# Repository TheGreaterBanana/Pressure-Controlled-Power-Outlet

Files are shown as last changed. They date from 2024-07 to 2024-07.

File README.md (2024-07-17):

# Pressure-Controlled-Power-Outlet
This is my (for sure) late Birthday present for my mom:

The idea for this project is that she have a water bin that holds water off of the roof of her house. Which my mother uses to water her gardens. The problem is that the pump she uses does not stop when the pressure starts to build!

So this is ment to fix this by using a water pressure sensor to see when the hose nozzel is closed by detecting a large jump in pressure then disablling the outlet that is powering the pump. Then when the nozzel is opened again this will detect the drop in pressure and re-enable the outlet.

This respository will have the code for the pico (RP2040) microcontroller, the schematics for the PCB and the case that will be used. 

The design philosophy for this project is to have everything as simple and cheap as possible, for this as many components as possible will be through hole as I dont want to pay to have parts placed on the pcb. If a part has to be surface mount it will have a extra large footprint to make it as easy as possible to assemble.

The specs:
    - 125V
    - 20A
    - GFCI protected outlets
    - Useable outdoors

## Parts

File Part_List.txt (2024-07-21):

This is the part list for the Pressure Controlled Power Outlet

digikey:
    Note: This is overkill but it was a 24V internal PSU that I had on hand
	Mornsun America LM100-23B24R2-C https://www.digikey.ca/en/products/detail/mornsun-america-llc/LM100-23B24R2-C/18108181 x1

HomeDepot:
    Leviton 20 Amp Self-Test SmartlockPro Slim Duplex GFCI Outlet https://www.homedepot.ca/product/leviton-20-amp-self-test-smartlockpro-slim-duplex-gfci-outlet-in-black/1001791826    x1

Mouser:
    Nichicon UCY2G120MPD 12µF Cap https://www.mouser.ca/ProductDetail/647-UCY2G120MPD                       x1
    STMicroelectronics LD1085V50 5V 3A LDO https://www.mouser.ca/ProductDetail/511-LD1085V50                x1
    TE Connectivity T9GS1L24-24 Relay https://www.mouser.ca/ProductDetail/655-T9GS1L24-24                   x1
    DFRobot SEN0257 Analog Water Pressure Sensor https://www.mouser.ca/ProductDetail/426-SEN0257            x2
    Io Audio IO-C20SP-63 C20 PEM https://www.mouser.ca/ProductDetail/670-IO-C20SP-63                        x1
    Raspberry Pi SC0918 Pico W https://www.mouser.ca/ProductDetail/358-SC0918                               x1
    Texas Instruments LM324AN/NOPB https://www.mouser.ca/ProductDetail/926-LM324AN-NOPB                     x1
    Vishay MBB02070C3302FCT00 33k Ohm Resistor https://www.mouser.ca/ProductDetail/594-MBB02070C3302FCT     x1
    YAGEO MFR-12FTF52-17K 17K Ohm Resistor https://www.mouser.ca/ProductDetail/603-MFR-12FTF52-17K          x1
    KOA Speer MF1/4LCT52R561G 560 Ohm Resistor https://www.mouser.ca/ProductDetail/660-MF1-4LCT52R561G      x4
    Infineon IRF540NPBF MOSFET https://www.mouser.ca/ProductDetail/942-IRF540NPBF                           x2
    Diotec Semiconductor 2N3906 Transistor https://www.mouser.ca/ProductDetail/637-2N3906                   x2
    Vishay 1N5405-E3/54 Diode https://www.mouser.ca/ProductDetail/625-1N5405-E3                             x2
    Phoenix Contact 1017514 PCB PWR Connector https://www.mouser.ca/ProductDetail/651-1017514               x1
    Diotec Semiconductor 2N3904 Transistor https://www.mouser.ca/ProductDetail/637-2N3904                   x4
    YAGEO MFR1WSFTE52-10K 10K Ohm Resistor https://www.mouser.ca/ProductDetail/603-MFR1WSFTE52-10K          x10
    Molex 47053-3000 4-Pin PWM Connector https://www.mouser.ca/ProductDetail/538-47053-3000                 x2
    Rubycon 80ZLH220MEFC10X23 220µF Cap https://www.mouser.ca/ProductDetail/232-80ZLH220MEFC10X2            x1
    KEMET ESL476M100AH9AA 47µF Cap https://www.mouser.ca/ProductDetail/80-ESL476M100AH9AA                   x1
    Harwin M7581-46 Jumper https://www.mouser.ca/ProductDetail/855-M7581-46                                 x2

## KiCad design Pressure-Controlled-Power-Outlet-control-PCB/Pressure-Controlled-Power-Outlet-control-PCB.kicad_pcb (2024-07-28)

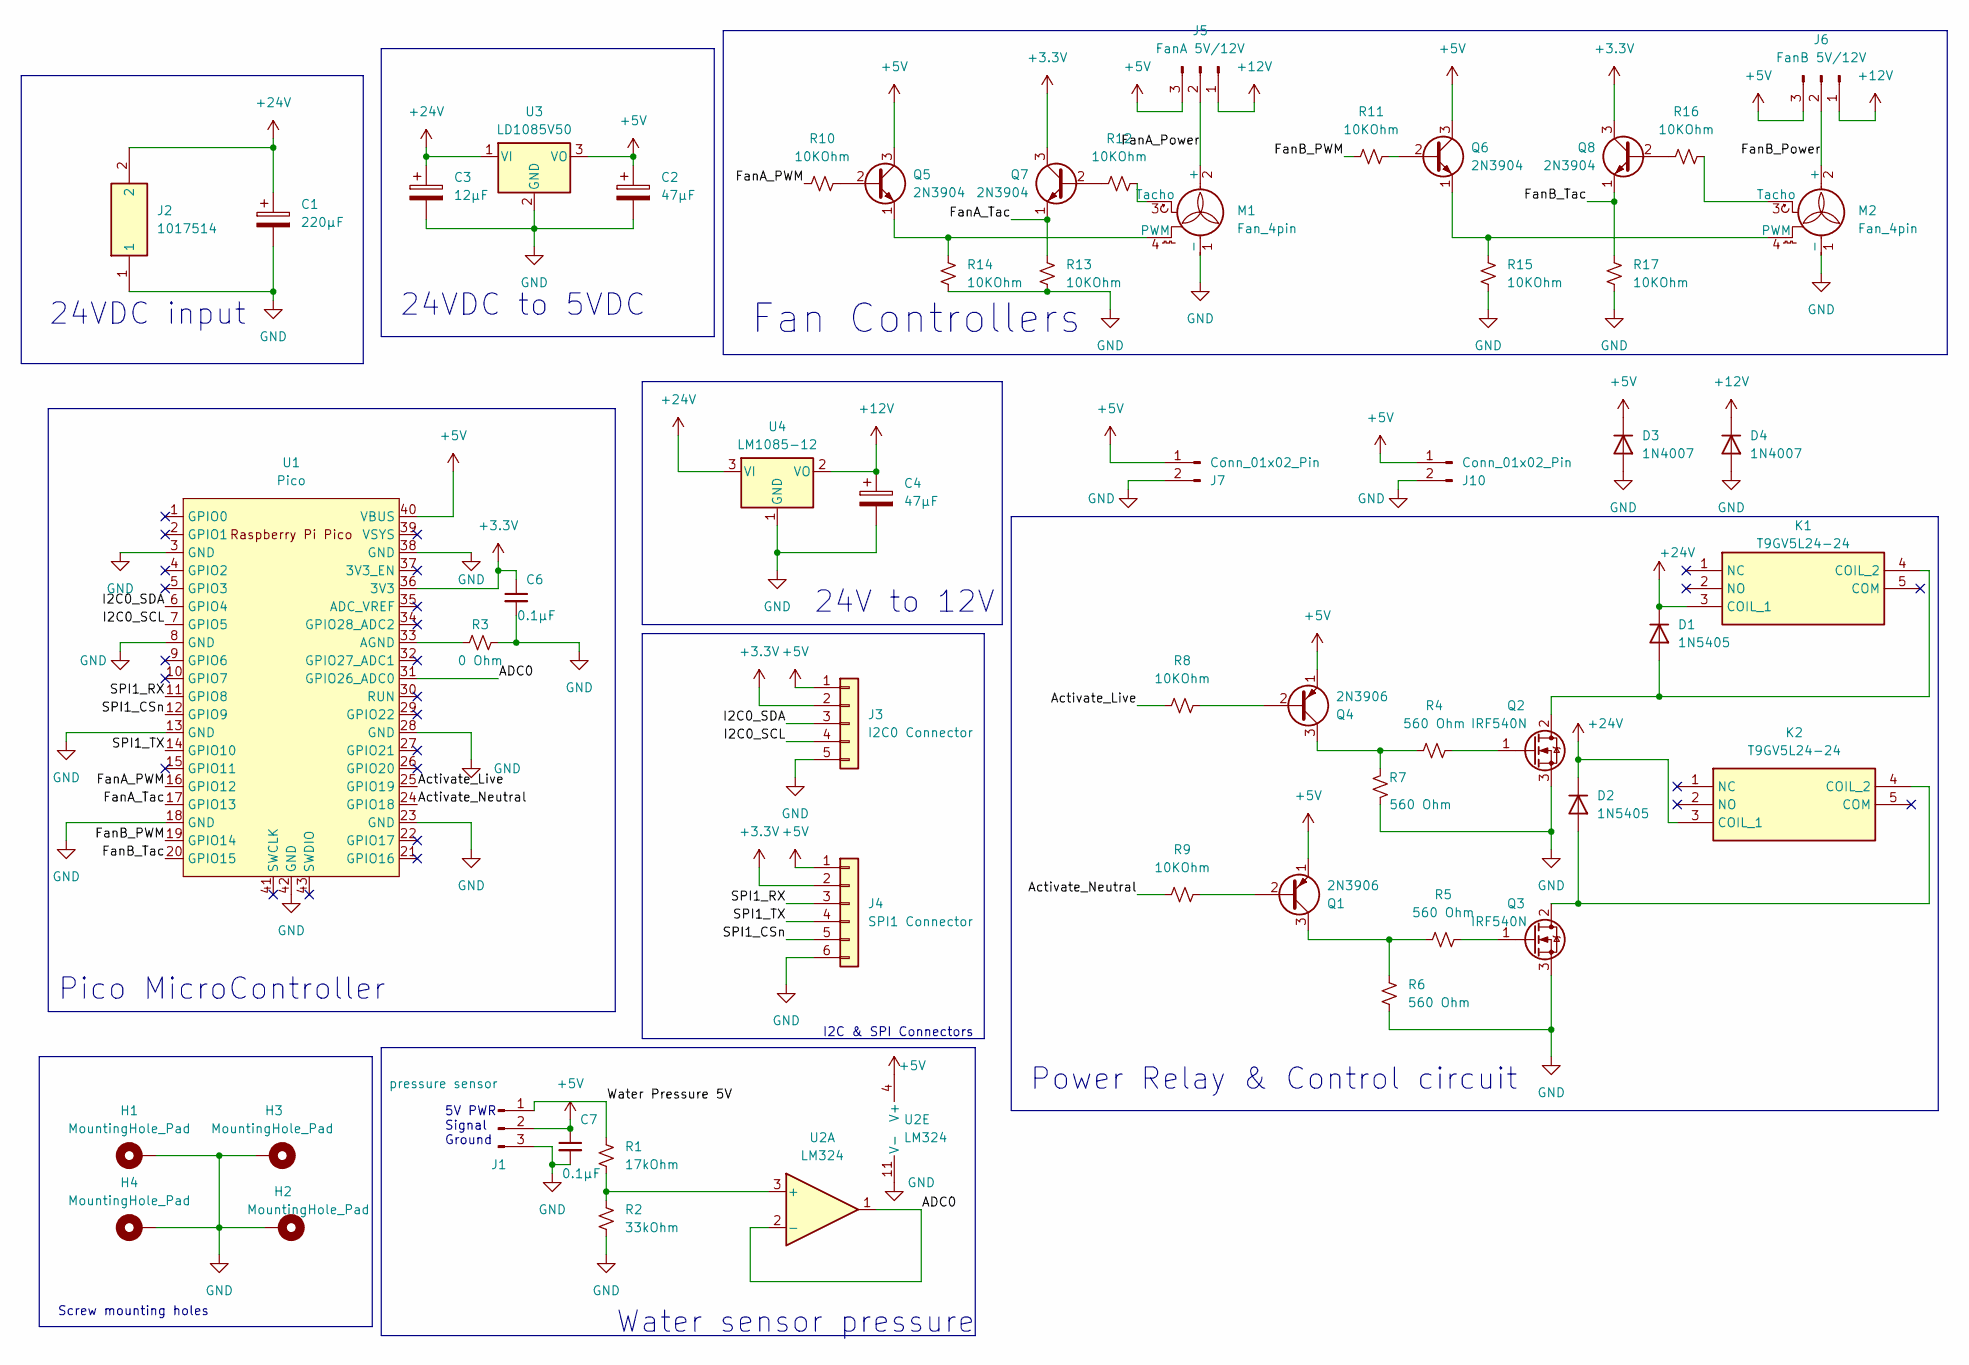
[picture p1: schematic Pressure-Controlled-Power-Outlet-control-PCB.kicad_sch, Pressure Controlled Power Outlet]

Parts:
C1: 220µF; CP_Radial_D10.0mm_P5.00mm
C2, C4: 47µF; CP_Radial_D10.0mm_P5.00mm
C3: 12µF; CP_Radial_D10.0mm_P5.00mm
C6, C7: 0.1µF; C_Rect_L7.2mm_W2.5mm_P5.00mm_FKS2_FKP2_MKS2_MKP2
D1, D2: 1N5405; D_DO-201AD_P15.24mm_Horizontal
D3, D4: 1N4007; D_DO-41_SOD81_P10.16mm_Horizontal
H1, H2, H3, H4: MountingHole_Pad; MountingHole_3.2mm_M3_ISO7380_Pad
J1: pressure sensor; PinHeader_1x03_P2.54mm_Vertical
J2: 1017514; Mouser Part Number 651-1017514
J3: I2C0 Connector; PinHeader_1x05_P2.54mm_Vertical
J4: SPI1 Connector; PinHeader_1x06_P2.54mm_Vertical
J5: FanA 5V/12V; PinHeader_1x03_P2.54mm_Vertical
J6: FanB 5V/12V; PinHeader_1x03_P2.54mm_Vertical
J7: Conn_01x02_Pin; JST_EH_B2B-EH-A_1x02_P2.50mm_Vertical
J10: Conn_01x02_Pin; PinHeader_1x02_P2.54mm_Vertical
K1, K2: T9GV5L24-24; T9GV5L2424; Mouser Part Number 655-T9GV5L24-24
M1, M2: Fan_4pin; FanPinHeader_1x04_P2.54mm_Vertical
Q1, Q4: 2N3906; TO-92_Inline
Q2, Q3: IRF540N; TO-220-3_Vertical
Q5, Q6, Q7, Q8: 2N3904; TO-92_Inline
R1: 17kOhm; R_Axial_DIN0207_L6.3mm_D2.5mm_P2.54mm_Vertical
R2: 33kOhm; R_Axial_DIN0207_L6.3mm_D2.5mm_P2.54mm_Vertical
R3: 0 Ohm; R_Axial_DIN0207_L6.3mm_D2.5mm_P2.54mm_Vertical
R4, R5, R6, R7: 560 Ohm; R_Axial_DIN0207_L6.3mm_D2.5mm_P2.54mm_Vertical
R8, R9, R10, R11, R12, R13, R14, R15, R16, R17: 10KOhm; R_Axial_DIN0207_L6.3mm_D2.5mm_P2.54mm_Vertical
U1: Pico; RPi_Pico_SMD_TH
U2: LM324
U3: LD1085V50; TO-220-3_Vertical
U4: LM1085-12; TO-220-3_Vertical

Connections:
+3.3V: C6.1, J3.2, J4.2, Q7.3 (C), Q8.3 (C), U1.36 (3V3)
+5V: C2.1, C7.1, D3.1 (K), J1.2, J3.1, J4.1, J5.3, J6.3, J7.1, J10.1, Q1.1 (E), Q4.1 (E), Q5.3 (C), Q6.3 (C), U1.40 (VBUS), U2.4 (V+), U3.3 (VO)
+12V: C4.1, D4.1 (K), J5.1, J6.1, U4.2 (VO)
+24V: C1.1, C3.1, D1.1 (K), D2.1 (K), J2.2, K1.3 (COIL_1), K2.3 (COIL_1), U3.1 (VI), U4.3 (VI)
/ADC0: U1.31 (GPIO26_ADC0), U2.1, U2.2 (-)
/Activate_Live: R8.1, U1.25 (GPIO19)
/Activate_Neutral: R9.1, U1.24 (GPIO18)
/FanA_PWM: R10.1, U1.16 (GPIO12)
/FanA_Power: J5.2, M1.2 (+)
/FanA_Tac: Q7.1 (E), R13.2, U1.17 (GPIO13)
/FanB_PWM: R11.1, U1.19 (GPIO14)
/FanB_Power: J6.2, M2.2 (+)
/FanB_Tac: Q8.1 (E), R17.2, U1.20 (GPIO15)
/I2C0_SCL: J3.4, U1.7 (GPIO5)
/I2C0_SDA: J3.3, U1.6 (GPIO4)
/SPI1_CSn: J4.5, U1.12 (GPIO9)
/SPI1_RX: J4.3, U1.11 (GPIO8)
/SPI1_TX: J4.4, U1.14 (GPIO10)
/Water Pressure 5V: J1.1, R1.2
GND: C1.2, C2.2, C3.2, C4.2, C6.2, C7.2, D3.2 (A), D4.2 (A), H1.1, H2.1, H3.1, H4.1, J1.3, J2.1, J3.5, J4.6, J7.2, J10.2, M1.1 (-), M2.1 (-), Q2.3 (S), Q3.3 (S), R2.2, R3.2, R6.1, R7.1, R13.1, R14.1, R15.1, R17.1, U1.3 (GND), U1.8 (GND), U1.13 (GND), U1.18 (GND), U1.23 (GND), U1.28 (GND), U1.38 (GND), U1.42 (GND), U2.11 (V-), U3.2 (GND), U4.1 (GND)
unnamed: D1.2 (A), K1.4 (COIL_2), Q2.2 (D)
unnamed: D2.2 (A), K2.4 (COIL_2), Q3.2 (D)
unnamed: M1.4 (PWM), Q5.1 (E), R14.2
unnamed: M1.3 (Tacho), R12.2
unnamed: M2.4 (PWM), Q6.1 (E), R15.2
unnamed: M2.3 (Tacho), R16.2
unnamed: Q1.2 (B), R9.2
unnamed: Q1.3 (C), R5.1, R6.2
unnamed: Q2.1 (G), R4.2
unnamed: Q3.1 (G), R5.2
unnamed: Q4.2 (B), R8.2
unnamed: Q4.3 (C), R4.1, R7.2
unnamed: Q5.2 (B), R10.2
unnamed: Q6.2 (B), R11.2
unnamed: Q7.2 (B), R12.1
unnamed: Q8.2 (B), R16.1
unnamed: R3.1, U1.33 (AGND)
unnamed: R1.1, R2.1, U2.3 (+)

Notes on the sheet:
Screw mounting holes
24VDC input
24V to 12V
Power Relay & Control circuit
5V PWR Signal Ground
Pico MicroController
Fan Controllers
I2C & SPI Connectors
24VDC to 5VDC
Water sensor pressure

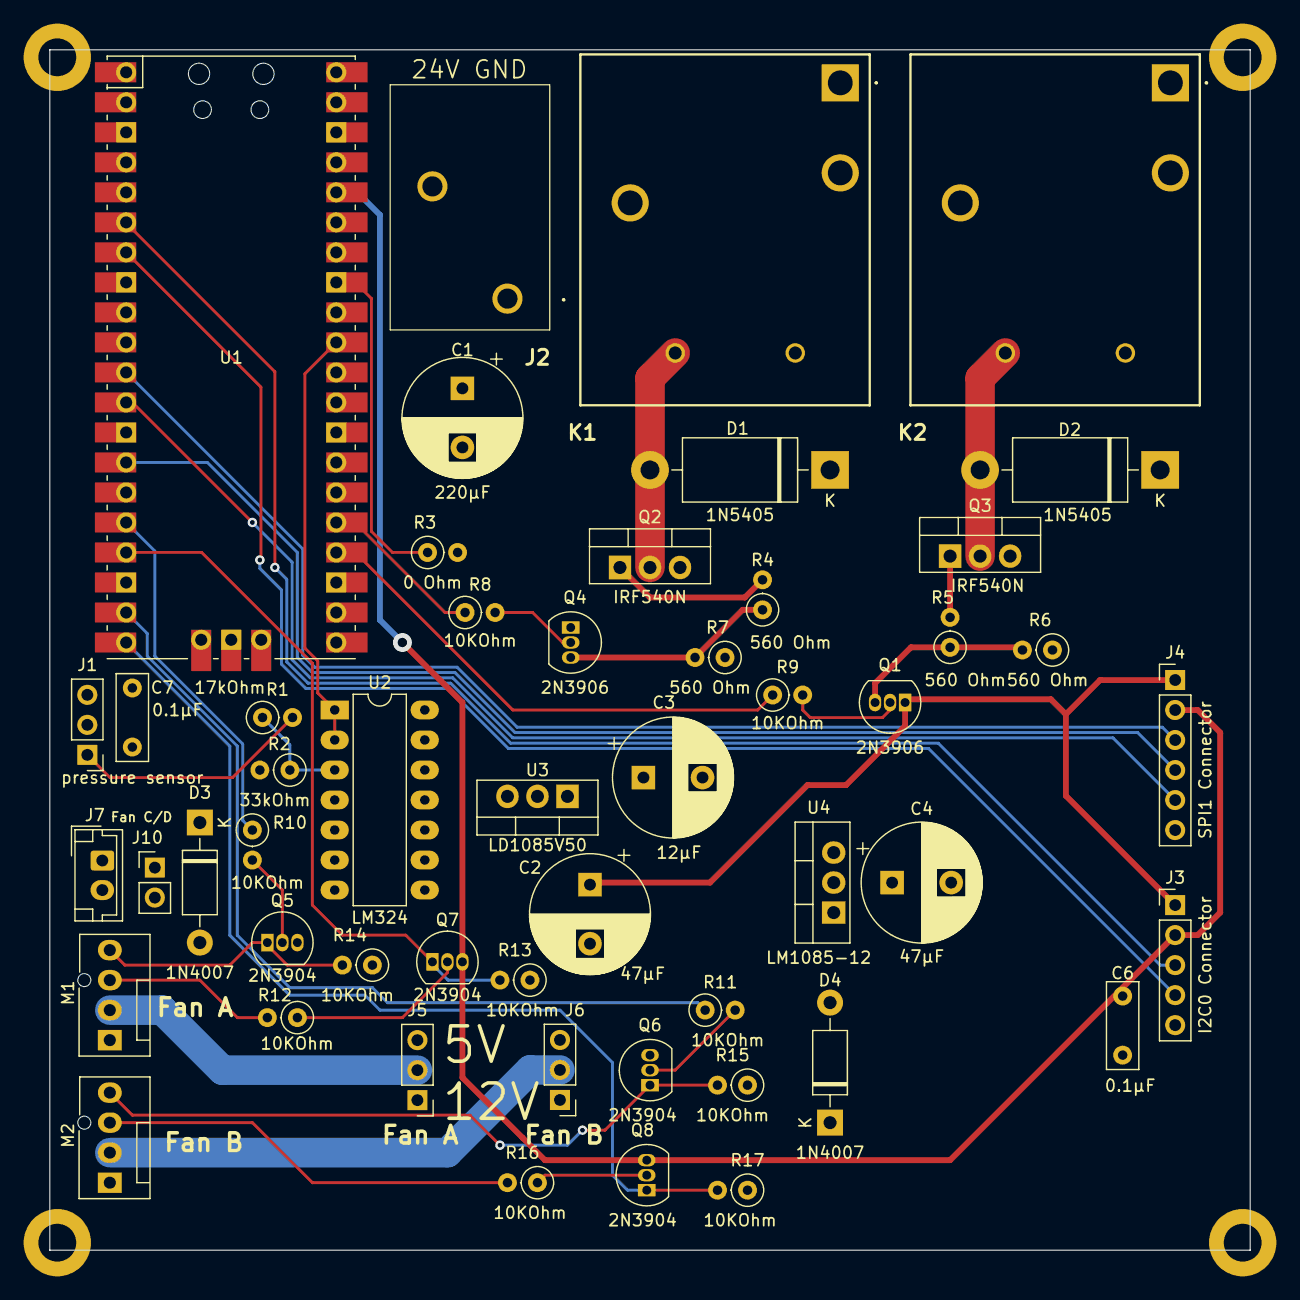
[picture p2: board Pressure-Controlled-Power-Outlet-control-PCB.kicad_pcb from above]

Board: 4 copper layers, 101.6 x 101.6 mm, 55 parts (0 on the bottom side), 38 nets.

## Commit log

2024-07-17 added control board KiCAD
    [Pressure-Controlled-Power-Outlet-control-PCB.kicad_pcb, Pressure-Controlled-Power-Outlet-control-PCB.kicad_sch]
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2024-07-17 Creating a 5V analog to 3.3V analog converter for SEN0257
    [Pressure-Controlled-Power-Outlet-control-PCB.kicad_sch]
2024-07-18 created a 5v logic to 3.3v logic for the water sensor
    [Pressure-Controlled-Power-Outlet-control-PCB.kicad_sch]
2024-07-18 have most of the traces ran on pcb but controlling the relays
    [Pressure-Controlled-Power-Outlet-control-PCB.kicad_pcb, Pressure-Controlled-Power-Outlet-control-PCB.kicad_sch]
2024-07-18 removed onboard power supply and replaced it with an external 24V PSU, and removed High voltage pcb connections as relays have connectors on the top of them
    [Pressure-Controlled-Power-Outlet-control-PCB.kicad_pcb, Pressure-Controlled-Power-Outlet-control-PCB.kicad_sch]
2024-07-18 wired PCB but the footprint does not match the relay im using so i need to swap the relay :(
    [Pressure-Controlled-Power-Outlet-control-PCB-B_Cu.gbr, Pressure-Controlled-Power-Outlet-control-PCB-B_Mask.gbr, Pressure-Controlled-Power-Outlet-control-PCB-B_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]
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2024-07-18 fixed PCB
    [Pressure-Controlled-Power-Outlet-control-PCB.kicad_pcb, Pressure-Controlled-Power-Outlet-control-PCB.kicad_sch]
2024-07-19 should be done need to review the board to ensure everything is good
    [Pressure-Controlled-Power-Outlet-control-PCB.kicad_pcb, Pressure-Controlled-Power-Outlet-control-PCB.kicad_sch]
2024-07-19 updated parts list with latest parts
    [Pressure-Controlled-Power-Outlet-control-PCB.kicad_pcb]
2024-07-19 removed grb files that where in the wrong spot
    [Pressure-Controlled-Power-Outlet-control-PCB-B_Cu.gbr, Pressure-Controlled-Power-Outlet-control-PCB-B_Mask.gbr, Pressure-Controlled-Power-Outlet-control-PCB-B_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]
2024-07-19 updated to use the sen0257 WPS
    [Pressure-Controlled-Power-Outlet-control-PCB-B_Cu.gbr, Pressure-Controlled-Power-Outlet-control-PCB-B_Mask.gbr, Pressure-Controlled-Power-Outlet-control-PCB-B_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]
2024-07-19 fixed PCB design to allow for better spacing of parts
    [Pressure-Controlled-Power-Outlet-control-PCB.kicad_pcb, Pressure-Controlled-Power-Outlet-control-PCB.kicad_sch]
2024-07-19 added a spi & I2C connector incase someone wants to add more sensors to the board
    [Pressure-Controlled-Power-Outlet-control-PCB.kicad_sch]
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2024-07-20 end of day save
    [Pressure-Controlled-Power-Outlet-control-PCB.kicad_pcb, Pressure-Controlled-Power-Outlet-control-PCB.kicad_sch]
2024-07-20 sign a new feature creep added two fan headers that can power ether 24 or 5 volt fans
    [Pressure-Controlled-Power-Outlet-control-PCB.kicad_pcb, Pressure-Controlled-Power-Outlet-control-PCB.kicad_sch]
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2024-07-20 hopefully final push for the day
    [Pressure-Controlled-Power-Outlet-control-PCB.kicad_pcb]
2024-07-20 hopefully final rev for the night
    [Pressure-Controlled-Power-Outlet-control-PCB.kicad_pcb]
2024-07-20 added name to pcb
    [Pressure-Controlled-Power-Outlet-control-PCB.kicad_pcb, Pressure-Controlled-Power-Outlet-control-PCB.kicad_sch]
2024-07-20 done for the day fixed some part spacing and traces
    [Pressure-Controlled-Power-Outlet-control-PCB.kicad_pcb]
2024-07-20 redid the fan controllers
    [Pressure-Controlled-Power-Outlet-control-PCB.kicad_pcb, Pressure-Controlled-Power-Outlet-control-PCB.kicad_sch]
2024-07-20 welp moved some stuff around
    [Pressure-Controlled-Power-Outlet-control-PCB.kicad_pcb]
2024-07-20 upgraded diodes to 1n5405 from 1n5401
    [Pressure-Controlled-Power-Outlet-control-PCB.kicad_pcb, Pressure-Controlled-Power-Outlet-control-PCB.kicad_sch]
2024-07-20 finished the through hole version of the board going to make a smd version for pick and place
    [Pressure-Controlled-Power-Outlet-control-PCB.kicad_pcb]
2024-07-20 added a copy that will be mostly surface mount components
    [Pressure-Controlled-Power-Outlet-control-PCB-B_Cu.gbr, Pressure-Controlled-Power-Outlet-control-PCB-B_Mask.gbr, Pressure-Controlled-Power-Outlet-control-PCB-B_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]
2024-07-20 make a quick version that has some SMD for pick and place
    [Pressure-Controlled-Power-Outlet-control-PCB.kicad_pcb, Pressure-Controlled-Power-Outlet-control-PCB.kicad_sch]
2024-07-21 added better longer lasting caps
    [Pressure-Controlled-Power-Outlet-control-PCB.kicad_pcb, Pressure-Controlled-Power-Outlet-control-PCB.kicad_sch]
2024-07-21 hopefully done this PCB
    [Pressure-Controlled-Power-Outlet-control-PCB.kicad_pcb, Pressure-Controlled-Power-Outlet-control-PCB.kicad_sch]
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2024-07-21 changed 24V fan power to 12V
    [Pressure-Controlled-Power-Outlet-control-PCB.kicad_pcb, Pressure-Controlled-Power-Outlet-control-PCB.kicad_sch]
2024-07-21 added 5v fan headers
    [Pressure-Controlled-Power-Outlet-control-PCB.kicad_pcb, Pressure-Controlled-Power-Outlet-control-PCB.kicad_sch]
2024-07-21 added some basic diodes to protect from fan feedback
    [Pressure-Controlled-Power-Outlet-control-PCB.kicad_pcb, Pressure-Controlled-Power-Outlet-control-PCB.kicad_sch]
2024-07-21 added some power filter caps
    [Pressure-Controlled-Power-Outlet-control-PCB.kicad_pcb, Pressure-Controlled-Power-Outlet-control-PCB.kicad_sch]
2024-07-21 :confounded: what is the pcb
    [Pressure-Controlled-Power-Outlet-control-PCB.kicad_pcb]
2024-07-21 moved some traces and components
    [Pressure-Controlled-Power-Outlet-control-PCB.kicad_pcb]
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2024-07-25 made a simple version of the pcb that does not have a microcontroller
    [Pressure-Controlled-Power-Outlet-control-PCB.kicad_pcb, Pressure-Controlled-Power-Outlet-control-PCB.kicad_sch]
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2024-07-25 created new updated PCB design that will fit the mount of the case
    [Pressure-Controlled-Power-Outlet-control-PCB.kicad_pcb, Pressure-Controlled-Power-Outlet-control-PCB.kicad_sch]
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2024-07-26 move smd and simple versions to a tangents folder
    [Pressure-Controlled-Power-Outlet-control-PCB.kicad_pcb, Pressure-Controlled-Power-Outlet-control-PCB.kicad_sch]
2024-07-26 added label to the PWR in to show the 24V and GND sides
    [Pressure-Controlled-Power-Outlet-control-PCB.kicad_pcb]
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
